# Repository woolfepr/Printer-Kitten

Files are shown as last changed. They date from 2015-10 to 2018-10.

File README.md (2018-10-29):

# Kitten
Portable, Accurate, Open Source 3D Printer

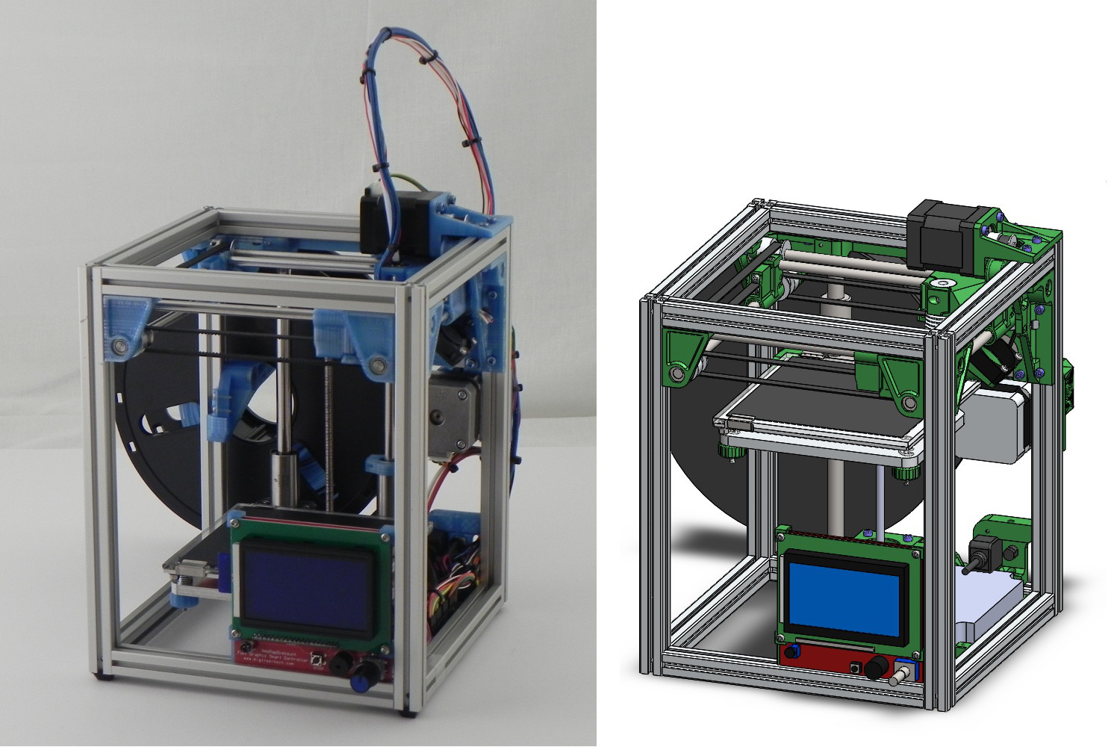
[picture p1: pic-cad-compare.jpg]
Comparing CAD model and real life Kitten Printer


## Printer Kitten Design Story
#### 3/31/16 - *Patrick Woolfenden*

The first printer I built was Sublime’s Tantillus. The Tantillus’ small size and print quality are what drew me to it. The Ultimaker Style X and Y axes motion system were fascinating. For me, the Tantillus turned out to be a great first printer. It wasn’t the easiest to put together and I had to source all of the parts myself, but in the end it didn’t disappoint delivering exceptional print quality.

Inspired by the Tantillus and the other T-Slot Tantillus and Ultimaker style printers, such as Brad Hill’s T-Slot Tantillus, Tim Rastall’s Ingentus, and Eric Lien’s HurcuLien, I set off to design my own version. This printer had a 200mm X 200mm print area and was roughly the same size as the Ultimaker. It used a 20mm extrusion frame, and toothed belts where the Tantillus had used high tension fishing line. After meeting Martin Bondėus at the 2015 MidWest RepRap Festival I decided to try the Bondtech extruder. It proved to be much more consistent and reliable than the Tantillus extruders I was used to. The printer worked well and produced great prints, but had its own set of issues. It remains unreleased, as I don’t think it’s ready for other people to try to build. It work well and had many unique design features that found their way to the Kitten.

The next printer I designed was the Kitten. Reflecting back to Midwest RepRap Festivals I had attended, I remembered how the Tantillus intrigued people because of its small compact design. I decided to make my next printer compact and portable.

I enjoyed the challenge of trying to package all of the printer components into the smallest and spatially efficient layout I could. In order to make the printer very compact the Kitten was first laid out with all of the X and Y-axes, print head, and frame purchased parts positioned in space. I iterated, trying different motor sizes and positions, rod diameters, bearing sizes, etc., keeping in mind that I would be designing printed parts to hold parts together. I decided on a 15mm T-slot extrusion [extruder or extrusion?], Nema 14, and E3D lite hot end. After feeling happy about the compact packaging layout, I began designing the printed part for the printhead. Once that was roughly designed I moved onto the rest of the X and Y-axes, making slight tweaks to the component layout as necessary. A clever way to tension the belts is key to the Kitten’s compact design. To fit in the small space available, hall effect switches are used for end stops. At this point I was confident that the frame foot print would be a 200mm square with a 100mm square print area. The X and Y-axes and printhead were the most challenging parts of the printer, with the goal of as small of a foot print as possible. 

For the Z-axis I opted for a simple cantilevered bed. 10mm rods and flanged linear bearings were used because they were the largest that could fit without increasing the size of the printer. Three oversized parts make the Kitten’s small bed very sturdy. A Nema 14 stepper motor with an integrated lead screw is used to move the bed. In order to keep it simple and stiff I decided to make the bed out of 2 metal plates. A silicone heated pad is used for bed heating. Leveling the bed is easy with 3 adjustment nuts. 

The Ultimachine mini-rambo was a great fit for the Kitten’s control electronics because of its ease of use, low profile, and small foot print. I stuck with the Bondtech V2 extruder for the Kitten. While the Kitten uses Nema 14 motors for the X, Y, and Z-axes, it still uses the standard Nema 17 for the extruder. I designed a pivoting spool holder that can be folded away to retain the Kitten’s small size for travel. Since the first Kitten, the printed parts have gone through many iterations. All of the printed parts of the Kitten have been designed so that printing without support material is possible. One part has a break way support modeled directly into the STL file. 

During the couple of months leading up to the 2016 Midwest RepRap Festival I built 2 more Kittens and made a kit for a friend, who built his own and provided me feedback. My friend Matt Skorina and I traveled to the Midwest RepRap Festival with 3 Kittens, reading to debut them to the 3D printing community.

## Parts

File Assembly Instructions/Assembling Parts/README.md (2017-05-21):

# Kitten Assembly Instructions

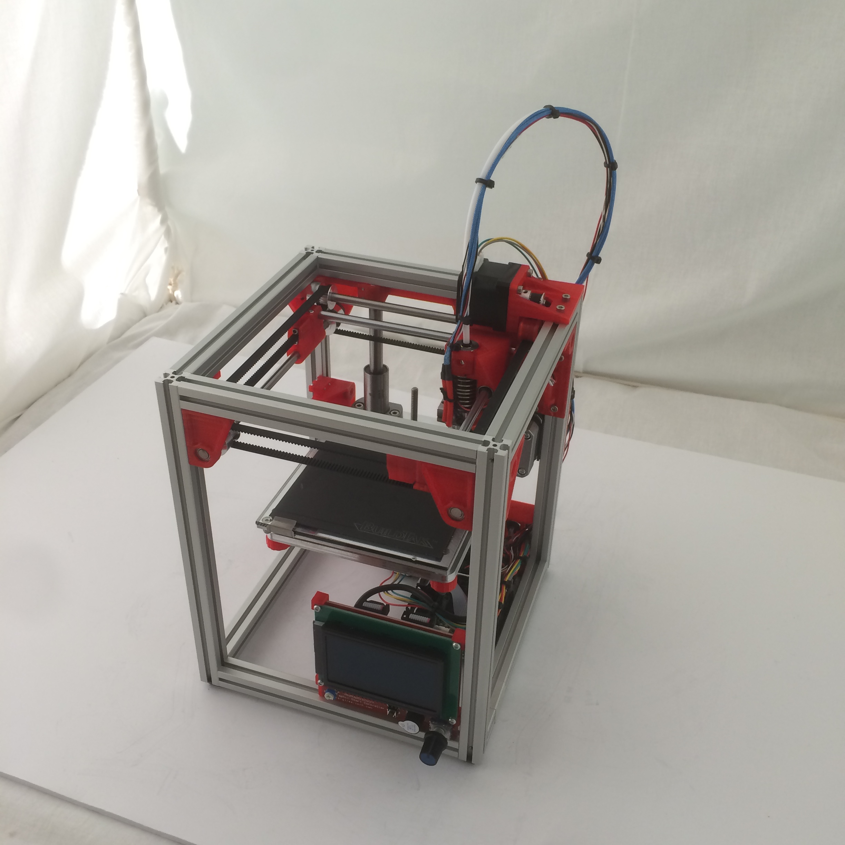
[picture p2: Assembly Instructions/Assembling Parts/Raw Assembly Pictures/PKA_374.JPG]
Assembly Picture


# Upper Back Right Corner

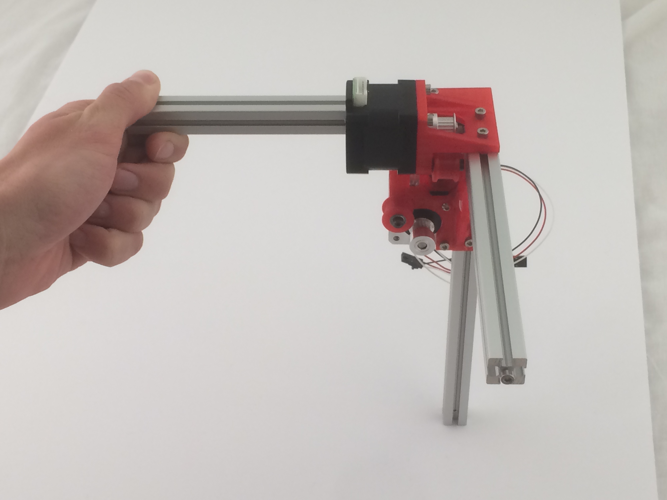
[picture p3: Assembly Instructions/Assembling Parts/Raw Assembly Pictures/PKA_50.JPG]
Assembly Picture


## Y End Stop

Upper back right printed part

Shorter end stop wire (1 of 2, mini rambo box)

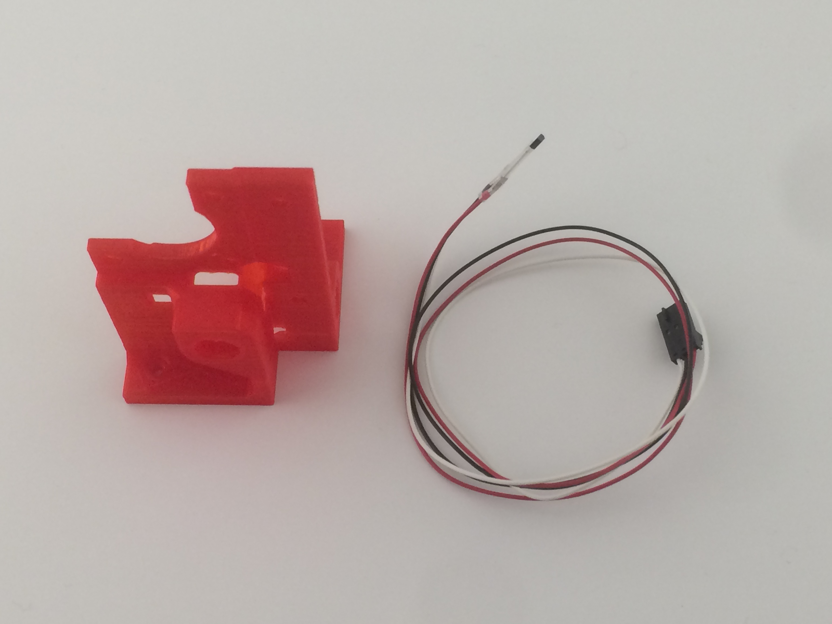
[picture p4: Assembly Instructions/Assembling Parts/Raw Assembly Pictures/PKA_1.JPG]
Assembly Picture


It is important the wire goes through the hole as shown

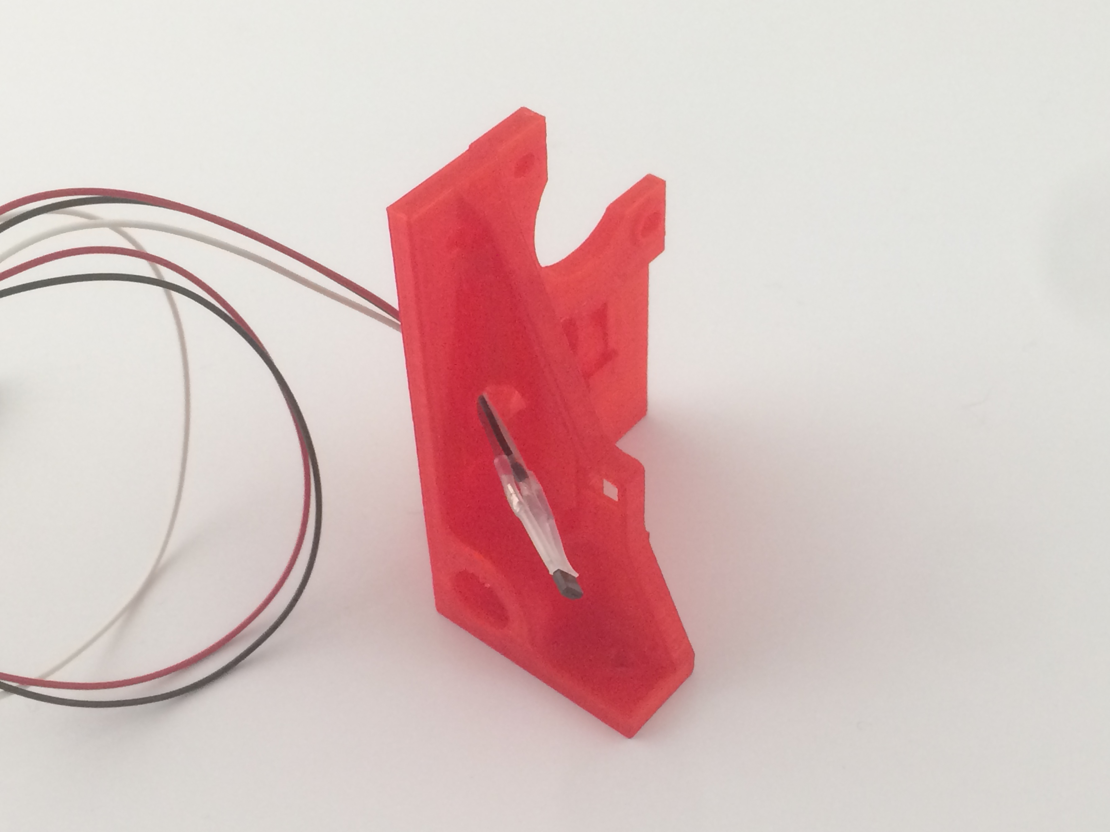
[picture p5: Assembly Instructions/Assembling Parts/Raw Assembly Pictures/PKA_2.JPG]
Assembly Picture


Feed through the other hole as shown

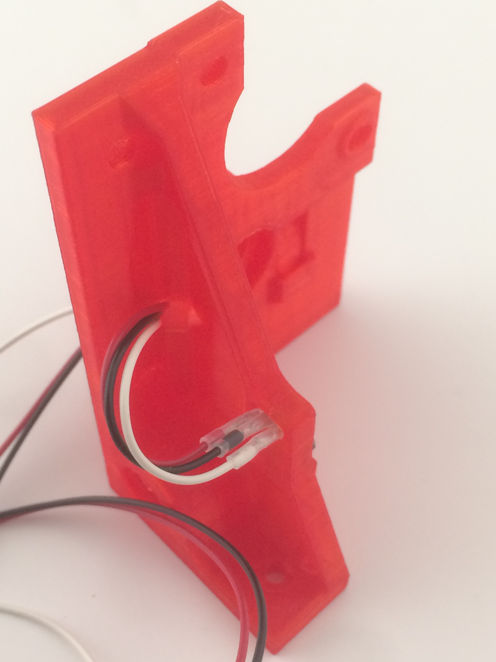
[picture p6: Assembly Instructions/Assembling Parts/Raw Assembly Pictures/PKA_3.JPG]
Assembly Picture


Orient the sensor so the smaller flat side (with text) is **not** against the plastic.

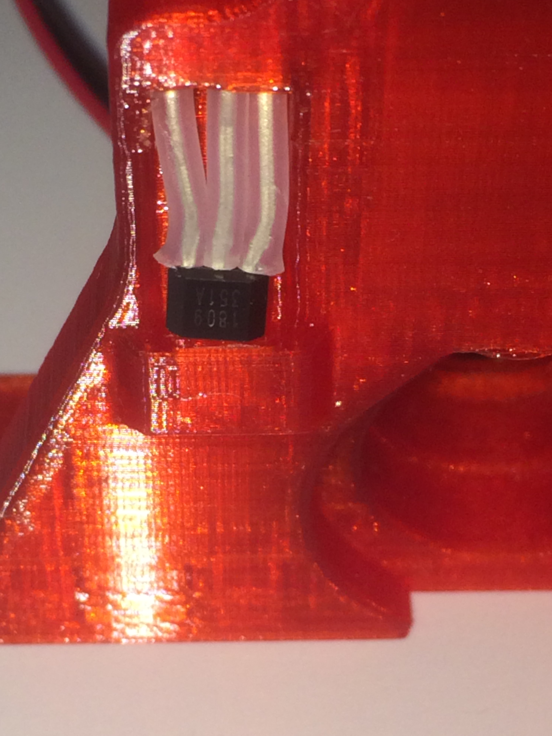
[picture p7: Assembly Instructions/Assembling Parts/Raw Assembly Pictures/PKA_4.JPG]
Assembly Picture


Push the sensor down until it is in the pocket. Use a drop of medium or thick viscosity super glue to glue the sensor in the pocket (recommended).

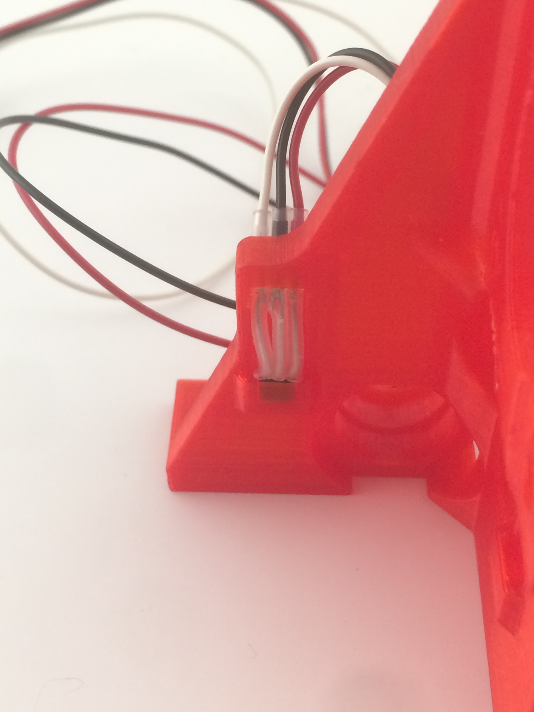
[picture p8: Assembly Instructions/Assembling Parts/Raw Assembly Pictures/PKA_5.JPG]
Assembly Picture


## X End Stop

Upper back right corner you just prepared

Shorter end stop wire (mini rambo box)

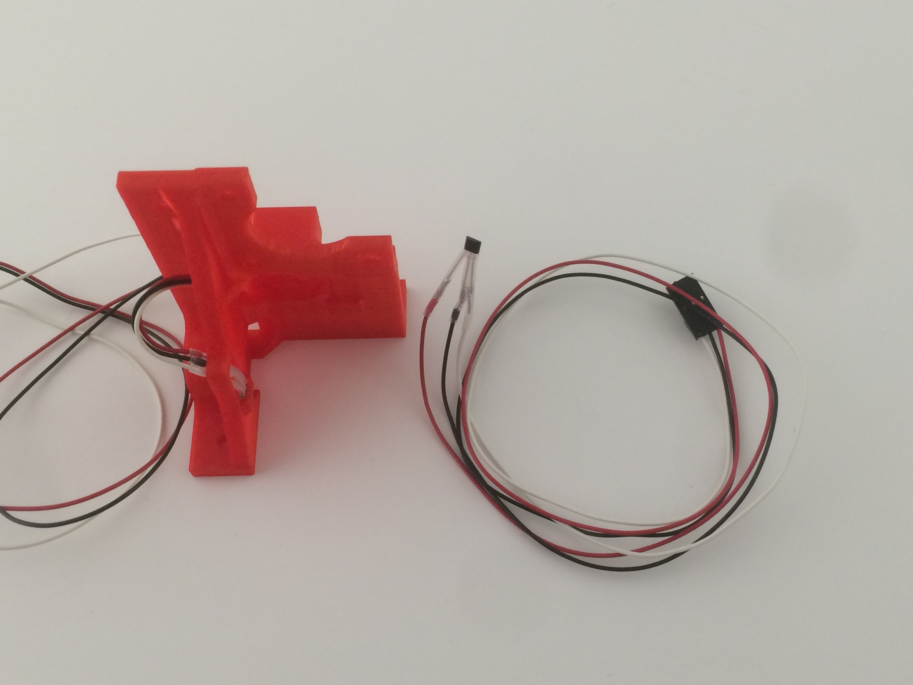
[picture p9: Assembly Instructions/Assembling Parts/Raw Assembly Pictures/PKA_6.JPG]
Assembly Picture


Feed the end stop sensor through this hole as shown.

Assembly Picture

Orient the sensor so the smaller flat side (with text) is **not** against the plastic.

Assembly Picture

Push the sensor down until it is in the pocket. Use a drop of medium or thick viscosity super glue to glue the sensor in the pocket (recommended).

## Bearings

Upper back right corner you just prepared

2 R188 bearings (larger bearing in bag 15)

Assembly Picture

Install bearings into the larger holes. Ensure bearings are fully seated. It can be helpful to press the bearings in with the back of a screwdriver.

Assembly Picture

## Frame Bolts

Upper back right corner you just prepared

5 M3x8 socket head cap screws (bag 1)

5 M3 square nuts (bag 11)

Assembly Picture

Place 5 screws in holes as shown and thread nuts onto them.

Assembly Picture

## Attach to Frame

Upper back right corner you just prepared

Longer extrusion

Assembly Picture

Slide extrusion along longest side of printed part. Feed the 3 nuts into the slots. Do not tighten the screws yet.

Assembly Picture

## Prepare Frame Rail

2 Shorter extrusion

4 M3x8 socket head cap screws (bag number 1)

Assembly Picture

Thread screws onto both end of rods. Leave about 2mm of spacing under screw cap.

Assembly Picture

## Make Frame Corner

Both shorter extrusions you just prepared

Longer extrusion attached to printed part you just prepared

(Picture omitted)

Slide shorter extrusion onto printed part as shown. Do not tighten the screws yet.

Assembly Picture

Slide the other shorter extrusion onto the remaining side and feed the one nut into the slots.

Assembly Picture

Slide the longer extrusion up so that the screw caps from the two shorter extrusions feed into the slots on the longer extrusion.

Assembly Picture

Use a 2.5mm allen key to tighten the screws in the extrusion. Insert the allen key through the drilled hole to tighten. As you tighten insure the extrusions are square and flush.

Assembly Picture

Tighten all 5 screws holding printed part on using the same 2.5mm allen key. Ensure part is flush with all 3 frame extrusions.

Assembly Picture

## X Axis Motor Thermal Pad

1 thermal pad (bag 19)

1 NEMA 14 motor (smaller motor)

Assembly Picture

Remover liner from both side of thermal pad and place on motor as pictured.

Assembly Picture

## X Axis Idler

2 684 bearings (smaller bearings in bag 15)

1 4mm spacer (bag 8)

1 M3 4x16 shoulder bolt (shorter bolt from bag 8)

1 Printed idler pulley

Assembly Picture

Put bearing into idler and slide shoulder bolt into bearing.

Assembly Picture

Put spacer onto the shoulder bolt so it is inside the idler.

Assembly Picture

Put bearing onto other side of idler

Assembly Picture

## Attach X Axis Motor

X Axis Motor you just prepared

Idler you just prepared

1 M3x8 button head cap screw (bag 3)

1 M3x8 socket head cap screw (bag 1)

Assembly Picture

Place motor as shown so thermal pad is against frame.

Assembly Picture 

Attach the idler as shown using a 2mm allen key.

Assembly Picture

Screw button head cap screw into hole as shown. Tighten with 2mm allen key.

Assembly Picture

Screw socket head cap screw into the remain hole. Tighten with 2.5mm allen key.

Assembly Picture 

## X Axis Motor Pulley

2 M3 set screws (bag 23)

1 16 tooth pulley (smaller pulley in bag 23)

Assembly Picture

Preinstall the set screws into the pulley as shown using 1.5mm allen key. It is recommended to use threadlock (Loctite Blue 242).

Assembly Picture

Slide pulley onto motor shaft aligning the belt guide with the idler and tighten.

Good

Assembly Picture

Bad

Assembly Picture

## Y Axis Idler

2 684 bearings (smaller bearings in bag 15)

1 4mm spacer (bag 8)

1 M3 4x20 shoulder bolt (longer bolt from bag 8)

1 Printed idler pulley

Assembly Picture

Put bearing into idler and slide shoulder bolt into bearing.

Assembly Picture

Put spacer onto the shoulder bolt so it is inside the idler.

Assembly Picture

Put bearing onto other side of idler

Assembly Picture

## Y Axis Motor Pulley

2 M3 set screws (bag 23)

1 16 tooth pulley (smaller pulley in bag 23)

1 NEMA 14 motor (smaller motor)

Assembly Picture 

Preinstall the set screws into the pulley as shown. It is recommended to use threadlock (Loctite Blue 242).

Assembly Picture

Install pulley onto motor. Do not tighten.

Assembly Picture

## Y Axis Motor Mounting

Y axis motor you just prepared

Y axis idler pulley you just prepared

3 M3x8 socket head cap screws (bag 1)

1 thermal pad (bag 19)

Y motor mount printed part

Assembly Picture

Place motor onto the printed part as shown and attach idler. Tighten idler with 2mm allen key. Make sure the connector is oriented as shown in the picture.

Assembly Picture

Screw 3 remaining socket head cap screws onto motor. Tighten with 2.5mm allen key.

Assembly Picture

Tighten pulley on motor shaft using 1.5mm allen key.  Ensure belt guide is aligned with idler.

Good

Assembly Picture

Bad

Assembly Picture

Remover liner from both side of thermal pad and place on motor as pictured.

Assembly Picture

## Attach Y Axis Motor Assembly

Y Axis Motor Assembly

3 M3x8 socket head cap screws (bag 1)

3 M3 square nuts (bag 11)

Assembly Picture 

Place Y motor assembly as shown.

Assembly Picture 

Slide nuts onto extrusion and align with holes on y axis motor assembly. Install screws and tighten each nut as it is aligned. It is helpful to use an allen key to slide the nut down the extrusion.

Assembly Picture

Assembly Picture 

# Upper Back Left Corner

Assembly Picture

## Z Axis Upper Rod Mount

3 M3x8 socket head cap screws (bag 1)

3 M3 square nuts (bag 11)

Z axis upper rod mount printed part

Assembly Picture 

Note that you use the correct printed part, correct part on left

Assembly Picture

Place screws in holes as shown and thread nuts onto them.

Assembly Picture

Slide assembly onto shorter extrusion as shown. The orientation of the part is important. Do not tighten.

Assembly Picture 

## Upper Back Left Corner

Upper back left corner printed part (listed as upper front right corner in BOM, but identical part)

4 M3x8 socket head cap screws (bag 1)

4 M3 square nuts (bag 11)

2 R188 bearings (larger bearing in bag 15)

Assembly Picture

Note that you use the correct printed part, good on left

Assembly Picture

Install bearings into the holes. Ensure fully seated.

Assembly Picture

Place screws in holes as shown and thread nuts onto them.

Assembly Picture

## Short Extrusion Sub Assembly

1 Shorter extrusion

2 M3x8 socket head cap screws (bag 1)

Assembly Picture

Thread screws onto both end of rod. Leave about 2mm of spacing under screw cap.

Assembly Picture

## Install Upper Back Left Corner

Shorter extrusion you just prepared

Upper back left corner you just prepared

Longer extrusion

Assembly Picture 

Slider longer extrusion along back corner of part. Feed the two nuts into the slots on the extrusion.

Assembly Picture

Slider the shorter extrusion along the part as shown. Feed the nut into the slot.

Assembly Picture

Slider the extrusion attached to the rest of the printer along the last remaining side. Feed the nut into the slot.

Assembly Picture 

Slide the longer extrusion up so that the screw caps from the two shorter extrusions feed into the slots on the longer extrusion. Use a 2.5mm allen key to tighten the screws in the extrusion. Insert the allen key through the drilled hole to tighten. As you tighten insure the extrusions are square and flush.

Assembly Picture

Tighten the four screws on the corner part with 2.5mm allen key. Ensuring the part is flush to all three extrusions.

Assembly Picture

Slide Z axis upper rod mount against the printer corner piece you just installed

Good

Assembly Picture 

Bad

Assembly Picture 

Tighten the three screws with 2.5mm allen key.

Assembly Picture

## Upper Front Right Corner

Assembly Picture

Upper Front Right Corner

Upper front right corner printed part

4 M3x8 socket head cap screws (bag 1)

4 M3 square nuts (bag 11)

2 R188 bearings (larger bearing in bag 15)

Assembly Picture

Note that you use the correct printed part, good on left

Assembly Picture

Install bearings into the holes. Ensure fully seated

Assembly Picture

Place screws in holes as shown and thread nuts onto them.

Assembly Picture

## Short Extrusion Sub Assembly

1 Shorter extrusion

2 M3x8 socket head cap screws (bag 1)

Assembly Picture

Thread screws onto both end of rod. Leave about 2mm of spacing under screw cap.

Assembly Picture 

## Install Upper Front Right Corner

Shorter extrusion you just prepared

Upper front right corner you just prepared

Longer extrusion

Assembly Picture 

Slider longer extrusion along back corner of part. Feed the two nuts into the slots on the extrusion.

Assembly Picture

Slider the shorter extrusion along the part as shown. Feed the nut into the slot.

Assembly Picture

Slider the extrusion attached to the rest of the printer along the last remaining side. Feed the nut into the slot.

Assembly Picture

Slide the longer extrusion up so that the screw caps from the two shorter extrusions feed into the slots on the longer extrusion. Use a 2.5mm allen key to tighten the screws in the extrusion. Insert the allen key through the drilled hole to tighten. As you tighten insure the extrusions are square and flush.

Assembly Picture

Tighten the four screws on the corner part with 2.5mm allen key. Ensuring the part is flush to all three extrusions.

Assembly Picture

# Upper Front Left Corner

Assembly Picture

## Upper Front Left Corner

Upper front left corner printed part

4 M3x8 socket head cap screws (bag 1)

4 M3 square nuts (bag 11)

2 R188 bearings (larger bearing in bag 15)

Assembly Picture

Install bearings into the holes. Ensure fully seated

Assembly Picture

Place screws in holes as shown and thread nuts onto them.

Assembly Picture 

## Install Upper Front Left Corner

Longer extrusion

Upper front left corner you just prepared

Assembly Picture 

Slider longer extrusion along back corner of part. Feed the two nuts into the slots on the extrusion.

Assembly Picture

Slide the assembly on the slot of the extrusion on the printer as shown.

Assembly Picture

Slide the remaining nut on the assembly onto the other extrusion on the printer.

Assembly Picture

Slide the longer extrusion up so that the screw caps from the two shorter extrusions feed into the slots on the longer extrusion. Use a 2.5mm allen key to tighten the screws in the extrusion. Insert the allen key through the drilled hole to tighten. As you tighten insure the extrusions are square and flush.

Assembly Picture

Tighten the four screws on the corner part with 2.5mm allen key. Ensuring the part is flush to all three extrusions.

(picture ommited)

# XY Axis Rods

Assembly Picture

## Rod Pulleys

8 20 tooth pulley (bag 23)

16 M3 set screws (bag 23)

Assembly Picture

Preinstall the set screws into the pulleys as shown using 1.5mm allen key.

Assembly Picture

## Magnets on XY Ends

2 xy end printed part

2 2mm x 1mm disc magnet (bag 13)

Assembly Picture

Glue magnets into the hole in the printed part as shown. Use medium or thick viscosity super glue.

Assembly Picture
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

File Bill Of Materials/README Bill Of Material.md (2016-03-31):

# Printer Kitten Bill of Materials

The bill of materials includes the parts required to build a Printer Kitten as well as recomended sources to buy them from.

Please keep in mind:
- Some of the items in the bill of materials are multiple of a certain part. This is most applicable to boxes of screws and other such hardware. If you order the recomended part number there will be extras of the part. Please keep this in mind if you plan to order parts for multiple printers.

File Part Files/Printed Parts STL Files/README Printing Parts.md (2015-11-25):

# Tips

If you plan on having a heated bed, I recommend not printing the print head out of PLA because of the fan shrouds proximity to the bed.

The parts for the extruder can be purchased from Bondtech. If you want to print your own, the files are available on the Bondtech website.

# Assemblies of Parts

The assemblies of parts can make it easier/faster to print Printer Kitten parts.
 
Printing all of the assemblies will make enough parts for a Kitten. 

The size of these assemblies are small enough to be printed on a Printer Kitten.

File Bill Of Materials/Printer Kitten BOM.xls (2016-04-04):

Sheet: Purchased Parts
Printer Kitten Purchased Parts
Part Description | Part# or SKU# | Estmated Cost Per Part | qty | ex cost | Source | Notes/ Recommendations
Motor, Stepper, NEMA14 X 44mm | MNEMA14-44 | $7.90 | 2 | $15.80 | robotdigg
Motor, Stepper, NEMA14 with Tr5*2 Acme Leadscrew | 14HY007-180T52 | $32.50 | 1 | $32.50 | robotdigg
Belt, GT2 6mm, Open Ended | GT2-6-OPEN | $1.80 | 2 | $3.60 | robotdigg | Order one 5-Meter Length for 3 printers
Fan, 25mm, 12V | E2510FAN | $1.80 | 1 | $1.80 | robotdigg
Motor, Stepper, Geared Nema17 | GNEMA17-34 | $27.00 | 1 | $27.00 | robotdigg
Pulley, GT2, 20 Tooth, 6.35mm Bore | GT2-20T-6.35B-6 | $1.85 | 8 | $14.80 | robotdigg
Pulley, GT2, 16 Teeth, 5mm Bore | GT2-16T | $1.80 | 2 | $3.60 | robotdigg | 5mm bore option
Bearing, 684ZZ, pack of 10 | BB683456 | $5.00 | 1 | $5.00 | Robotdigg | You will use 4 of these bearings
Screw, M3 x 8mm Socket Cap, Pack of 25 | SCS-M3-08 | $0.62 | 3 | $1.86 | trimcraftavationrc | You will use about 62 of these screws
Screw, M3 x 8mm Flat, Pack of 25 | 336 | $0.45 | 1 | $0.45 | trimcraftavationrc | You will use 4 of these screws
Screw, M3 x 8mm Button, pack of 25 | BSC_M3_8 | $0.61 | 1 | $0.61 | trimcraftavationrc | You will use 1 of these screws
Screw, M4 x 8mm Socket Cap, pack of 25 | SCS-M4-08 | $0.90 | 1 | $0.90 | trimcraftavationrc | You will use 4 of these screws
Screw, 4-40 x .625 Socket Cap, pack of 25 | SCS-440X5/8 | $0.47 | 1 | $0.47 | trimcraftavationrc | You will use 4 of these screws
Screw, 4-40 x 1.25 Socket Cap, pack of 12 | 147 | $0.49 | 1 | $0.49 | trimcraftavationrc | You will use 4 of these screws
Nut, M3, pack of 25 | PHN-M3 | $0.24 | 1 | $0.24 | trimcraftavationrc | You will use 6 of these nuts
Nut, M3 Lock, pack of 25 | NYLK-M3 | $0.39 | 1 | $0.39 | trimcraftavationrc | You will use 4 of these nuts
Washer, M3, pack of 25 | FW-M3 | $0.14 | 1 | $0.14 | trimcraftavationrc | You will use 3 of these washers
Washer, M3 Split Lock, pack of 25 | SLW-M3 | $0.16 | 1 | $0.16 | trimcraftavationrc | You will use 3 of these washers
Heat Shrink Tubing, 1/16" 1 foot | HST-1-16 | $0.49 | 1 | $0.49 | trimcraftavationrc | This is for the endstop hall switches
Screw, M3 x 30mm Flat, pack of 25 | 92125A140 | $5.06 | 1 | $5.06 | McMaster | You will use 3 of these screws
Screw, M2.63-1.06 X 10mm Torx, pack of 50 | 99397A416 | $9.92 | 1 | $9.92 | McMaster | You will use about 20 of these screws
Screw, M2.63-1.06 X 14mm Torx, pack of 50 | 99397A583 | $11.78 | 1 | $11.78 | McMaster | You will use about 24 of these screws
Screw, Shoulder M3 4 x 16 | 92981A144 | $2.35 | 1 | $2.35 | McMaster
Screw, Shoulder M3 4 x 20 | 92981A145 | $2.39 | 1 | $2.39 | McMaster
Spacer, 4 x 4mm | 94669A006 | $1.25 | 2 | $2.50 | McMaster
Spring, pack of 12 | 9657K288 | $10.35 | 1 | $10.35 | McMaster | You will usae 3 of these springs
Bumper, pack of 50 | 95495K24 | $5.85 | 1 | $5.85 | McMaster | You will use 4 of these bumpers
Glass, 5" x 5" x .125" | 8476K15 | $12.63 | 1 | $12.63 | McMaster
O-Ring, 011 Viton, pack of 100 | 9464K16 | $6.32 | 1 | $6.32 | McMaster | You will use 1 of these O-rings
Zip Tie, 4", pack of 100 | 7130K52 | $2.43 | 1 | $2.43 | McMaster
Shaft, 10mm | SFJ10-210 | $8.44 | 2 | $16.88 | misumi
Shaft, 6mm | PSFJ6-164 | $6.60 | 2 | $13.20 | misumi
Bearing, Linear, 6 x 10 x 35mm | LMKW6 | $13.35 | 2 | $26.70 | misumi | I do not recommend buying cheap Chineese linear bearings.
Bearing, Linear, flange, 10 x 19 x 47mm | LHICD10 | $9.82 | 2 | $19.64 | misumi | I do not recommend buying cheap Chineese linear bearings.
Nuts, Square, m3, pack of 100 | HNSQ3-3 | $8.28 | 1 | $8.28 | misumi | You will use about 32 of these nuts
Frame, Aluminum, 3 series 240mm | HFS3-1515-240 | $2.64 | 4 | $10.56 | misumi
Frame, Aluminum, 3 series 170mm | HFS3-1515-170 | $2.64 | 8 | $21.12 | misumi
Shaft, 0.25 X 7.75in | U-SFJ0.25-L7.75 | $4.20 | 4 | $16.80 | misumi
Mini-Rambo 1.3 | UMMINIRAMBOPAC13 | $120.00 | 1 | $120.00 | ultimachine | get with Optical Endstop Kits w/ Wiring so you get the correct endstop wires
Hot End, E3D Lite6 Full Kit - 1.75mm Universal (with Bowden add-on) (12v) | NA | $40.00 | 1 | $40.00 | e3d-online
Extruder, Bondtech, V2 1.75 Mechanical Kit | NA | $60.00 | 1 | $60.00 | Bondtech | shop.Bondtech.se
Adapter Direct - Bowden 1.75 | NA | $7.90 | 1 | $7.90 | Bondtech | shop.Bondtech.se
Omnipolar Hall Switch | AH1809-P-B-ND | $0.76 | 3 | $2.28 | digikey
Thermal Pad, Gap Pad GP1500-0.060 | BER228-ND | $39.76 | 1 | $39.76 | digikey | You will have lots of extra if you buy this sheet of thermal pad. Less expensive cut to size pads will be available on printerkitten.com
Full Graphic Smart LCD Controller | 12864LCD | $69.00 | 1 | $69.00 | reprapdiscount | You can find this for a much better price just be wary of the quality of knock offs
USB B Extension, 30cm, Female to Male, Panel Mount, 90°Right Angle | NA | $3.00 | 1 | $3.00 | aliexpress | You want to make sure you are getting the correct style
Bed Clip, UM2 | NA | $2.00 | 3 | $6.00 | aliexpress
Bearing, R188 | R188-ZZ | $3.75 | 8 | $30.00 | bocabearings | Less expensive high quality bearings are available, but Boca Bearings will for sure be good
Heater Pad, with Thermister, 4"X4", 100W 12V | NA | $24.99 | 1 | $24.99 | ebay user Keenovo | (Optional) ebay user Keenovo
DC Power Jack, Panel Mount, 5.5mm x 2.1mm, pack of 15 | NA | $6.99 | 1 | $6.99 | ebay user weisschang2011 | you only need one of these
Power Supply, 12V | NA | $30.00 | 1 | $30.00 | ebay | >5Amp no heated bed , >12Amp with 100watt bed, >9Amp 50watt bed
N50. 3mm x 1 mm Disc Magnet | D1007 | $0.19 | 3 | $0.57 | SuperMagnetMan
BuildTak, 4.5" x 4.5" Square, Black (Pack of 3) | NA | $9.35 | 1 | $9.35 | Amazon
Z-Axis Frame | NA | $50.00 | 1 | $50.00 | machine shop? | This is one 1 of 2 not off the shelf parts for the printer. Will be available on printerkitten.com Drawings are available if you wish to source/make your own.
Z-Axis Bed | NA | $50.00 | 1 | $50.00 | machine shop? | This is one 1 of 2 not off the shelf parts for the printer. Will be available on printerkitten.com Drawings are available if you wish to source/make your own.
 | Total Purchased Parts Cost |  |  | $864.90
Usefull tools you may consider buying
Torx L-Key, T8 | 6959A14 | $2.13 | 1 | $2.13 | McMaster | This is usefull for the plastic threadforming screws

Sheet: Printed Parts
Printed Parts
File name | Qty
Printed Part, Corner, Upper Front Right | 2
Printed Part, Corner, Upper Back Right | 1
Printed Part, Corner, Upper Front Left | 1
Printed Part, Y Motor Mount | 1
Printed Part, Z Axis Upper Rod Mount | 1
Printed Part, Z Axis Lower Rod Mount | 1
Printed Part, Z End Stop Magnet Mount | 1
Printed Part, Z End Stop Mount | 1
Printed Part, Z Motor Mount | 1
Printed Part, BondTech Clamp 1 | 1
Printed Part, BondTech Clamp 2 | 1
BondTech Housing V2 Front 1.75 | 1
BondTech Housing V2 Rear | 1
Printed Part, Z Adjustment Nut | 3
Printed Part, IO Mount | 1
Printed Part, X&Y End | 4
Printed Part, Print Head Body | 1
Printed Part, Print Head Clamp | 1
Printed Part, Spool Holder Part1 | 1
Printed Part, Spool Holder Part4 | 1
Printed Part, Spool Holder Part2 | 1
Printed Part, Spool Holder Part3 | 1
Printed Part, LCD Mount 1 | 1
Printed Part, LCD Mount 2 | 1
Printed Part, LCD Mount 3 | 1
Printed Part, LCD Mount 4 | 1
Printed Part, Rambo Mini Mount 1 | 2
Printed Part, Rambo Mini Mount 2 | 1
Printed Part, X&Y Belt Guide | 2
Printed Part, X&Y Spacer | 8
Printed Part, X&Y End Belt Clamp 1 | 4
Printed Part, X&Y End Belt Clamp 2 | 4
Printed Part, X&Y End Belt Clamp 3 | 4
total Printed parts | 57

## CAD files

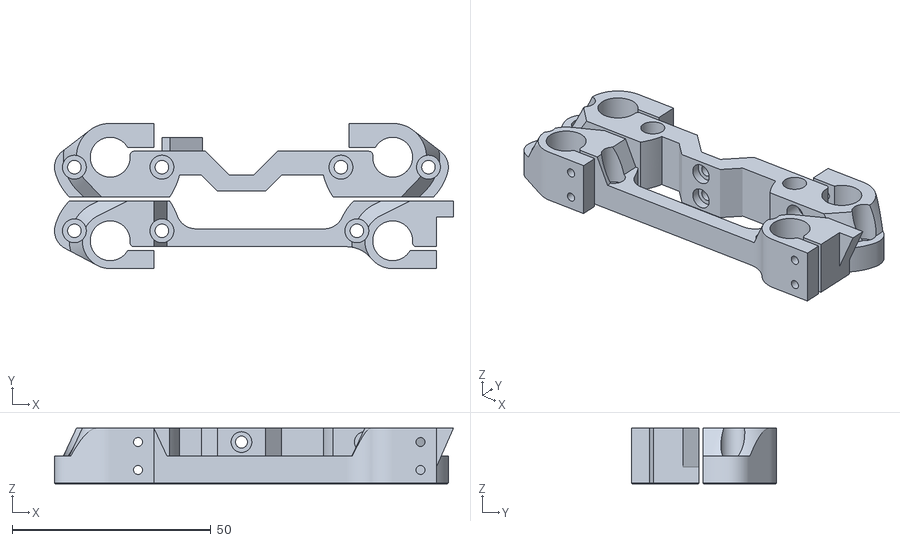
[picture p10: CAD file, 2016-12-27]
Part Files/Printed Parts STL Files/Assemblies of Parts/Print Assembly 3 Z Axis.STL
100.3 x 36.5 x 14.0

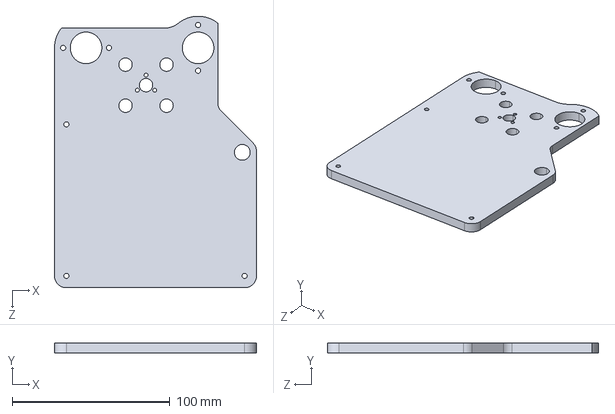
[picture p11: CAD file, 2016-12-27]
Part Files/Bed Plates/Z Axis Frame REV2.IGS
128.0 x 6.35 x 172.0 mm

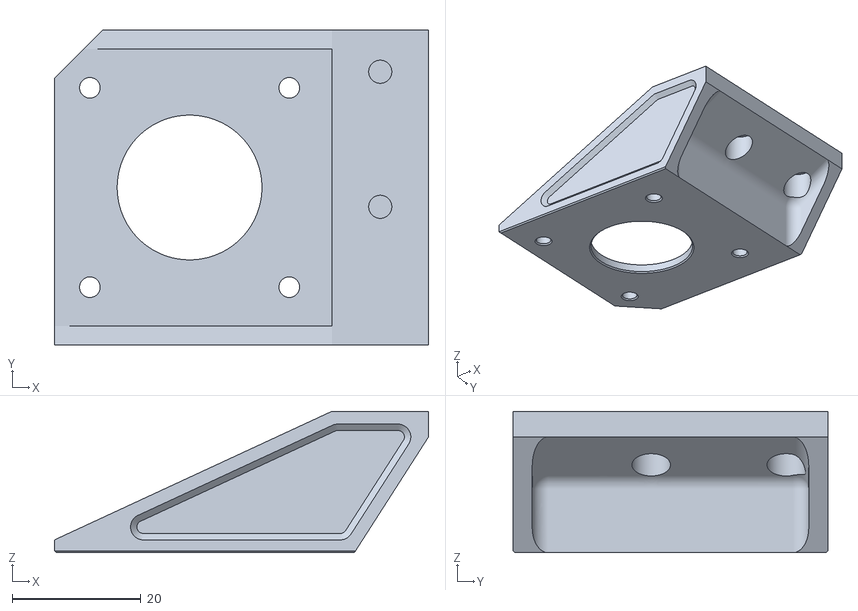
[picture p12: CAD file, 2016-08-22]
Part Files/Printed Parts STL Files/Printed Part, Titan Mount.STL
58.2 x 49.0 x 22.0

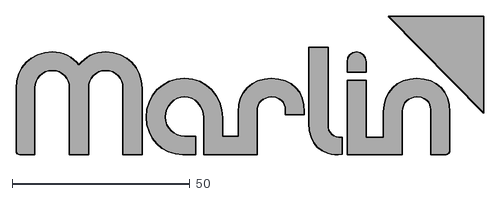
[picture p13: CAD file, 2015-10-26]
Software/Firmware/Marlin-1.0.2-Printer-Kitten/Documentation/Logo/Marlin Logo.dxf
131.6 x 39.5

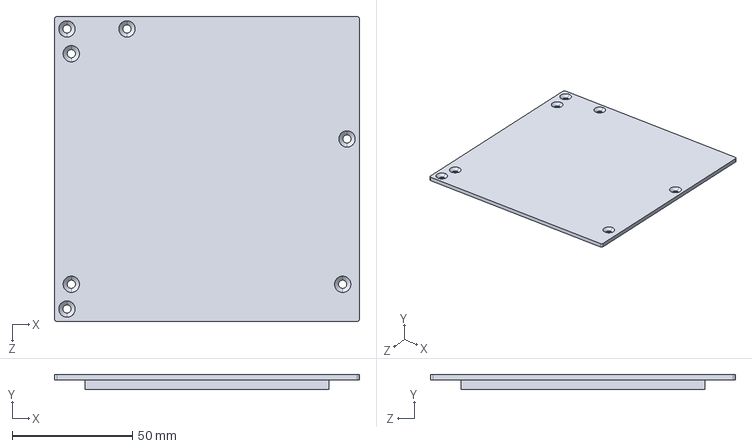
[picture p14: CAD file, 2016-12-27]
Part Files/Bed Plates/Z Axis Bed REV3.IGS
127.0 x 6.35 x 127.0 mm

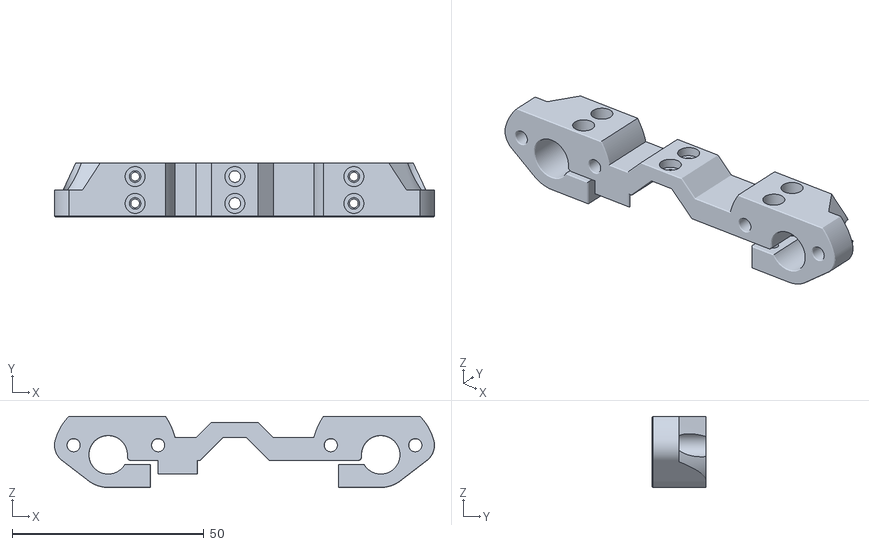
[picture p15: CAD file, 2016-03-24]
Part Files/Printed Parts STL Files/Printed Part, Z Axis Lower Rod Mount.STL
99.0 x 14.0 x 18.5

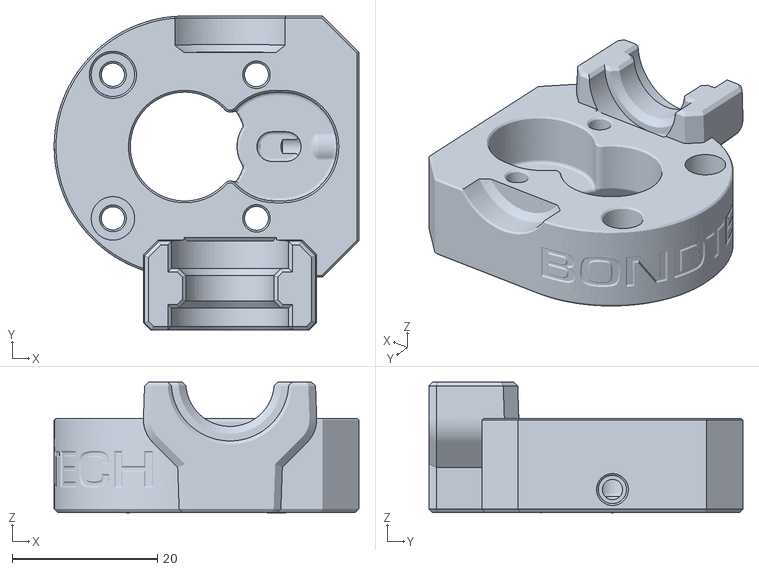
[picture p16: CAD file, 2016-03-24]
Part Files/Printed Parts STL Files/Bondtech Housing V2 Rear.STL
42.0 x 43.3 x 18.0

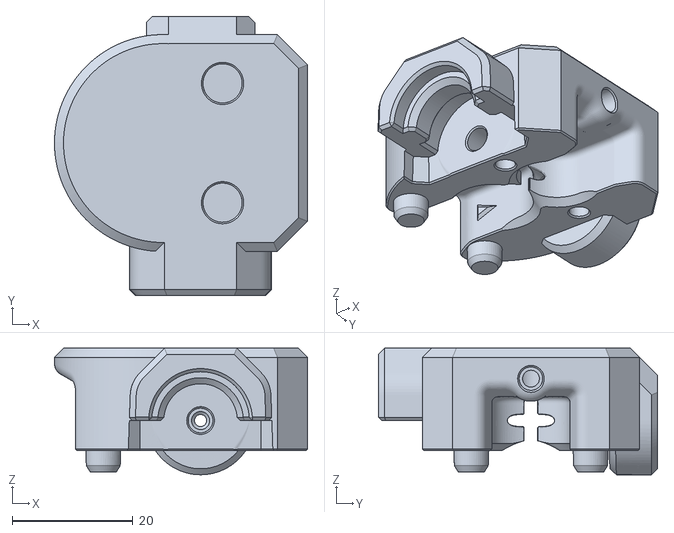
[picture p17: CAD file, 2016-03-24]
Part Files/Printed Parts STL Files/Bondtech Housing V2 Front 1.75.STL
42.0 x 46.3 x 21.0

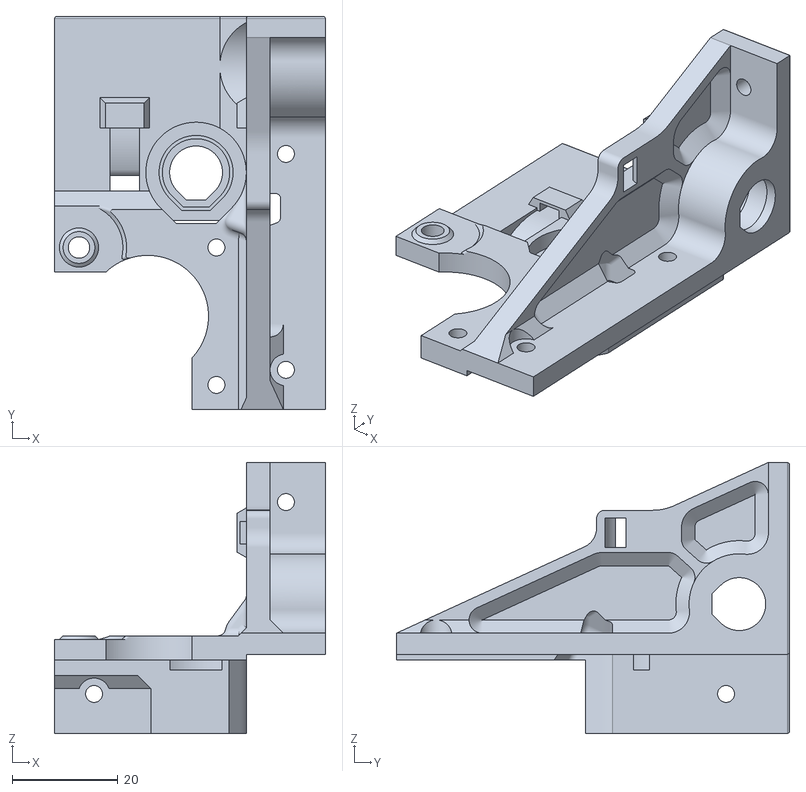
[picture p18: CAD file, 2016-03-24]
Part Files/Printed Parts STL Files/Printed Part, Corner, Upper Back Right.STL
51.3 x 74.3 x 51.3

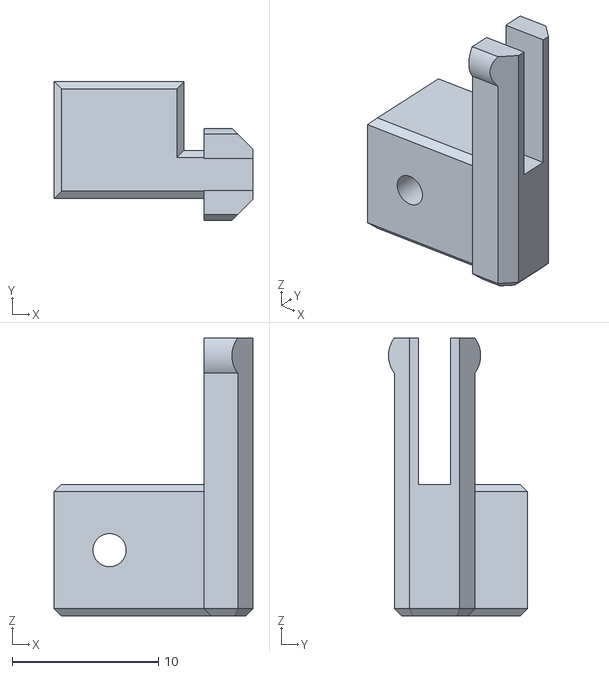
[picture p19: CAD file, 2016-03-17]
Part Files/Printed Parts STL Files/Printed Part, Rambo Mini Mount 1.STL
13.6 x 9.50 x 19.0

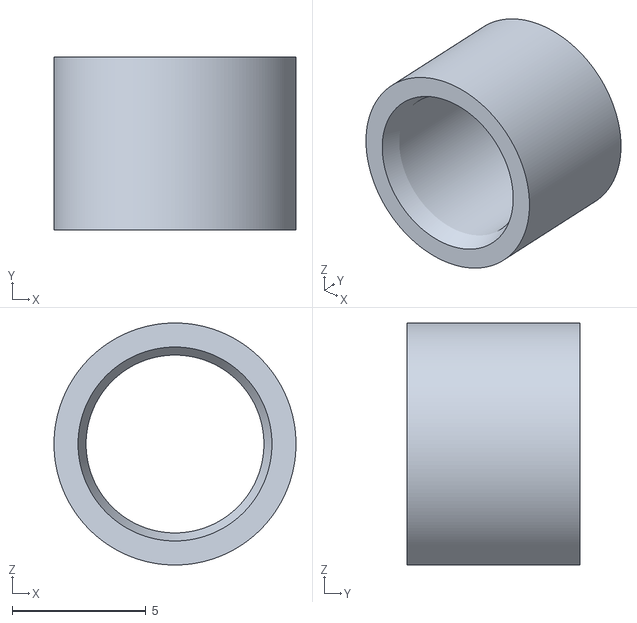
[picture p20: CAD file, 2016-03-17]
Part Files/Printed Parts STL Files/Printed Part, X&Y Spacer.STL
9.05 x 6.49 x 9.05

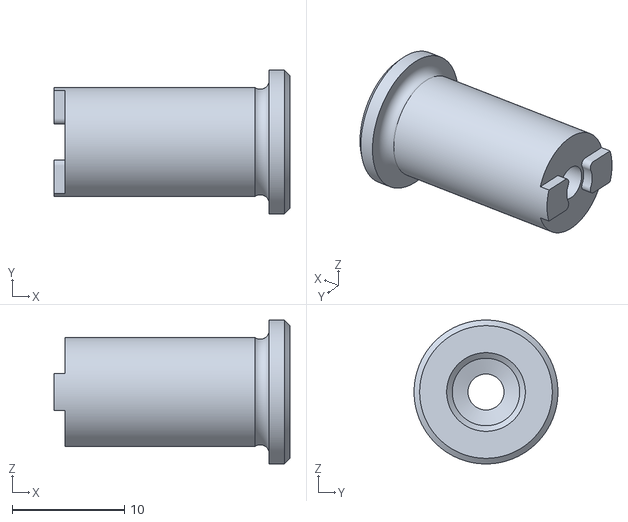
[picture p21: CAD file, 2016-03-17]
Part Files/Printed Parts STL Files/Printed Part, Spool Holder Part4.STL
21.0 x 12.8 x 12.8

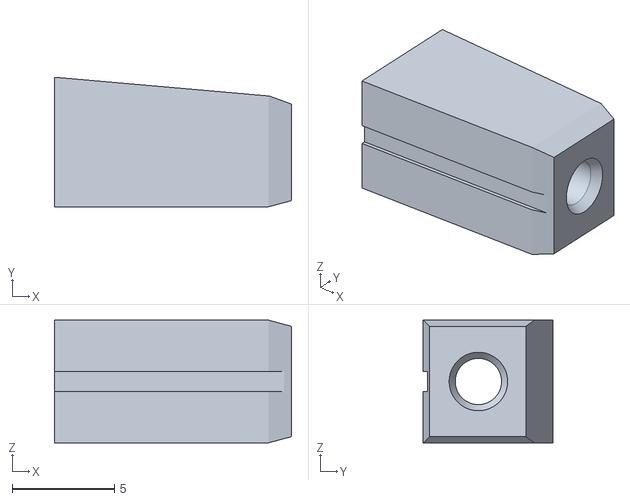
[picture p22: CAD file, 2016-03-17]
Part Files/Printed Parts STL Files/Printed Part, X&Y End Belt Clamp 1.STL
11.6 x 6.34 x 6.00

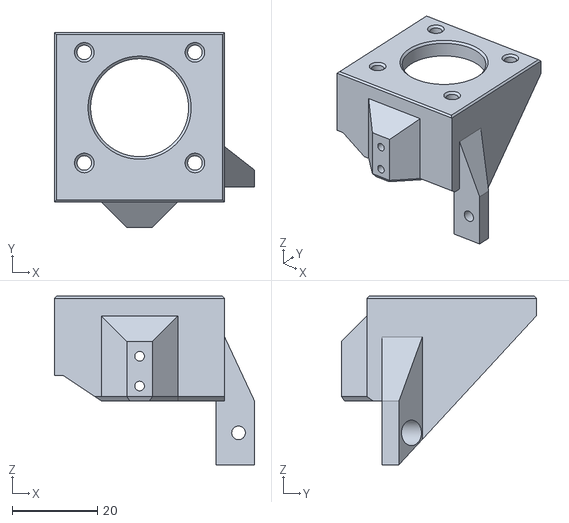
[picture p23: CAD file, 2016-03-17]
Part Files/Printed Parts STL Files/Printed Part, Z Motor Mount.STL
47.0 x 45.8 x 39.6

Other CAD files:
Part Files/Printed Parts STL Files/Printed Part, IO Mount.STL
Part Files/Printed Parts STL Files/Printed Part, Corner, Upper Front Left.STL
Part Files/Printed Parts STL Files/Printed Part, Print Head Clamp.STL
Part Files/Printed Parts STL Files/Printed Part, Z End Stop Magnet Mount.STL
Part Files/Bed Plates/Z Axis Bed REV3.x_t
Part Files/Bed Plates/Z Axis Frame REV2.x_t
Part Files/Printed Parts STL Files/Printed Part, BondTech Clamp 1.STL
Part Files/Printed Parts STL Files/Printed Part, BondTech Clamp 2.STL
Part Files/Printed Parts STL Files/Printed Part, Corner, Upper Front Right.STL
Part Files/Printed Parts STL Files/Printed Part, LCD Mount 1.STL
Part Files/Printed Parts STL Files/Printed Part, LCD Mount 2.STL
Part Files/Printed Parts STL Files/Printed Part, LCD Mount 3.STL
Part Files/Printed Parts STL Files/Printed Part, LCD Mount 4.STL
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

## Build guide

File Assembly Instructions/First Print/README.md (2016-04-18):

# First Print

## Load your PLA filament

Manually move the bed down so the nozzle is not to close to the bed

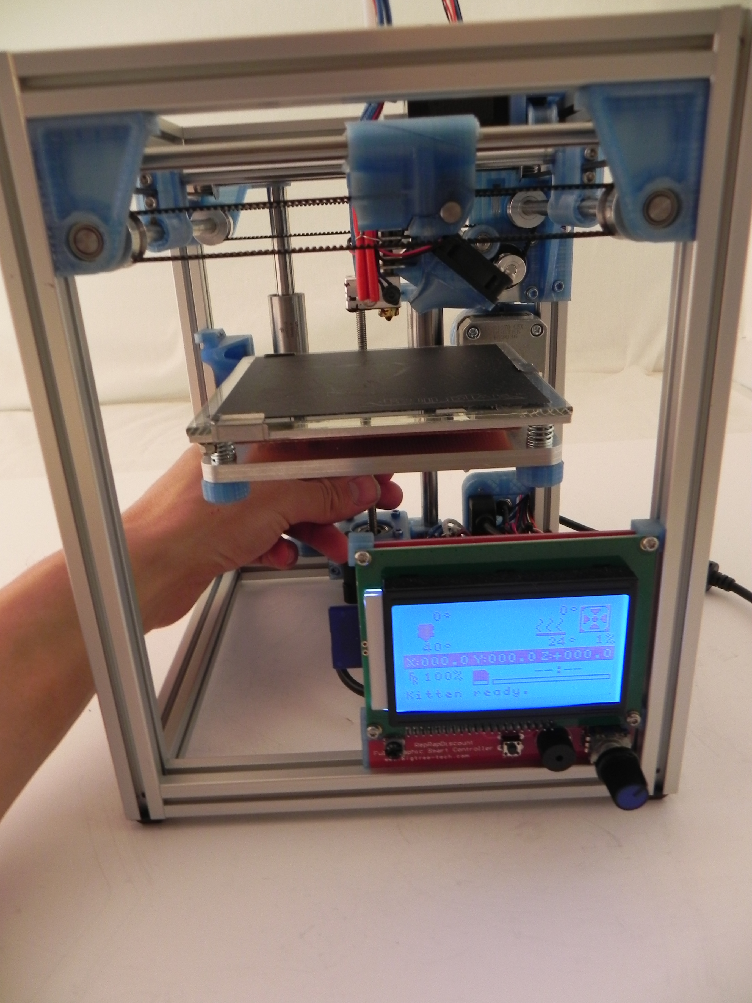
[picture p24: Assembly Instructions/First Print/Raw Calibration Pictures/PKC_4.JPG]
Calibration Picture


Preheat the nozzle by navigating on the LCD controller to prepare, then preheat PLA, then preheat PLA 1. Wait until the nozzle is up to more than 180 degrees C.

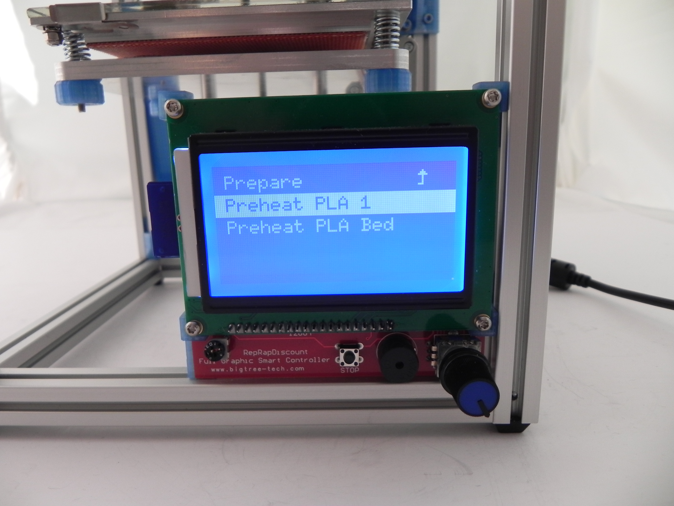
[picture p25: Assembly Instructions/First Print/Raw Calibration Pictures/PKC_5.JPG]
Calibration Picture


Cut off the tip of the filament if needed (if the end of the filament is not clean, is bent, or has a molten blob).  Mount the spool on the spool holder and feed the tip of the filament into the bottom of the extruder.

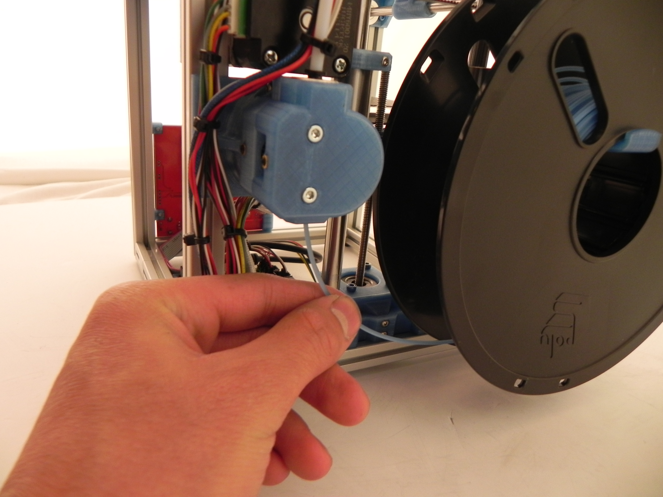
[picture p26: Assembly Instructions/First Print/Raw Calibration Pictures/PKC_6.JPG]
Calibration Picture


Holding the filament into the extruder, navigate on the LCD to prepare, and then load filament. The extruder should feed the filament up through the Bowden tube.

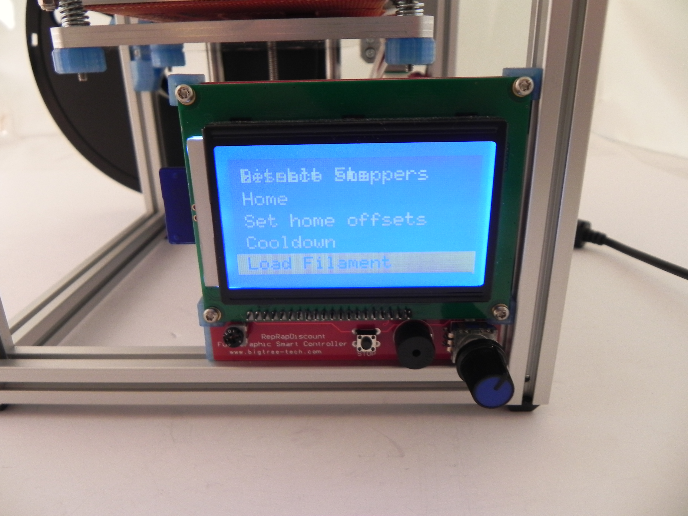
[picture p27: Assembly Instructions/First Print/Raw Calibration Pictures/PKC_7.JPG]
Calibration Picture


Navigate to prepare, then purge 5mm on the LCD. Purge 5mm until the filament is flowing smoothly out of the nozzle. (It doesn’t hurt to purge a little more than you probably need  in order to ensure all the air bubbles in the nozzle have come out)

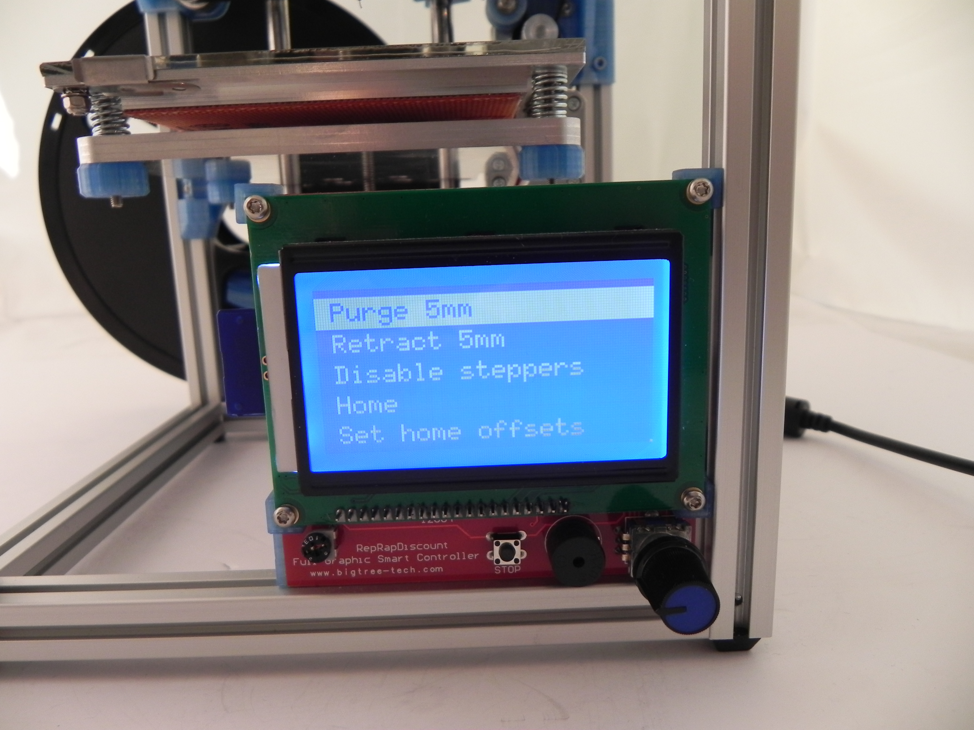
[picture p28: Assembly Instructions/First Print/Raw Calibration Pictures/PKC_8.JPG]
Calibration Picture


Navigate to prepare, then cooldown.

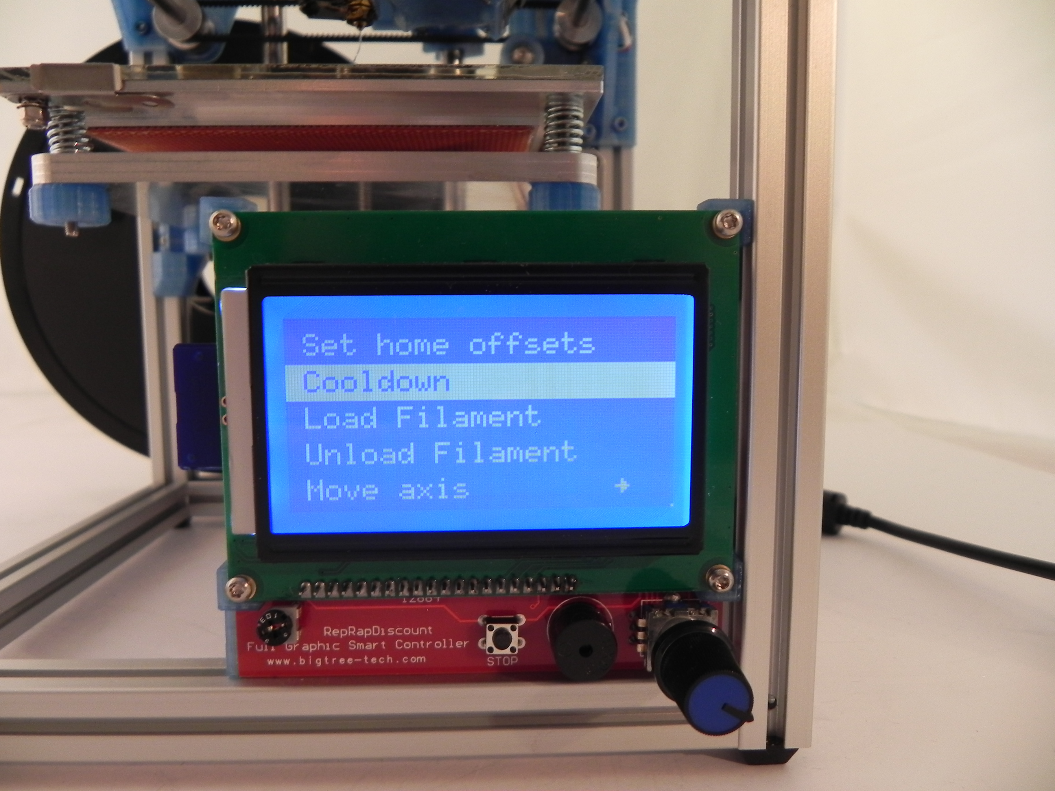
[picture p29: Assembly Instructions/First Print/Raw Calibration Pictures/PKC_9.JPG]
Calibration Picture


## First Print

There is gcode file (no slicer needed) ready to go for a first print. [FirstPrint_3DBenchy.gcode](https://github.com/woolfepr/Printer-Kitten/blob/master/Assembly%20Instructions/First%20Print/FirstPrint_3DBenchy.gcode) Simply put it on the SD card, navigate to print from SD, and select it. Your printer should heat up and successfully print for the first time.

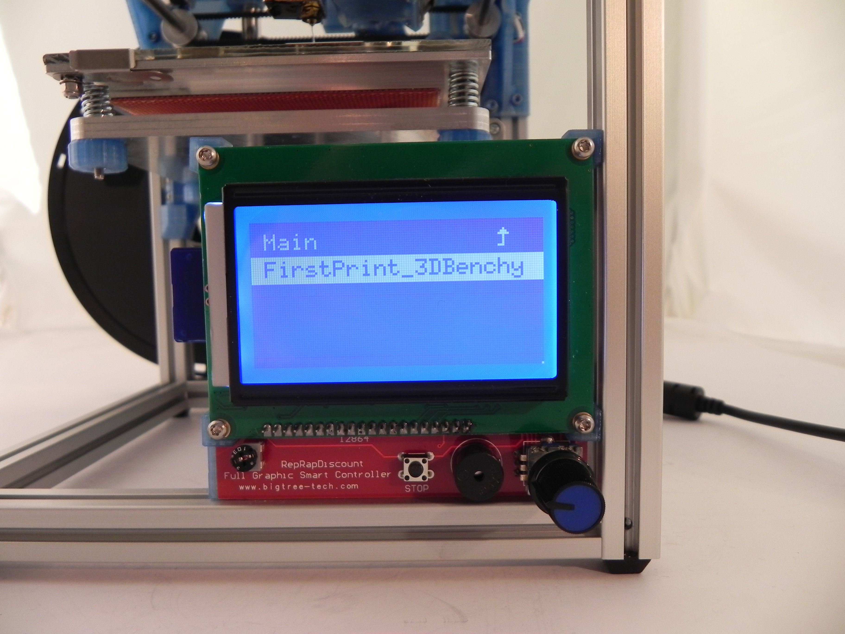
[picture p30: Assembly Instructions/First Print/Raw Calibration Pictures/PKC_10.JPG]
Calibration Picture


Once the first print is finished and you are ready to print items of your own choice or design you will need to begin using a slicer/ tool pathing program. I recommend using [Cura by Ultimaker](https://ultimaker.com/en/products/cura-software). Download and install the latest version.

The profile I have fine-tuned to run PLA on the kitten is available on Github. [Kitten 1.75.ini](https://github.com/woolfepr/Printer-Kitten/blob/master/Software/Cura%20Profile/Kitten%201.75.ini)  This profile should be a good starting point as far as tuning. You will want to play with the settings in order to get the best results on different models.

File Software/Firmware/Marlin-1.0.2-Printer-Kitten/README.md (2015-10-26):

Current Status: Bug Fixing
===================

What bugs are we working on: https://github.com/MarlinFirmware/Marlin/milestones/Bug%20Fixing%20Round%201

IRC channel on freenode: #marlin-firmware

(baaaah, #marlin was taken)

If a google hangout is needed then use this link: 

https://plus.google.com/hangouts/_/event/cps5d0ru0iruhl6ebqbk9dpqpa4?authuser=0&hl=da

It's valid for the next 10 years, must remember to renew then :-P

Developer Notes
===================

- There are now 2 branches: The __development__ branch is where new features and code changes will be sorted out. This branch may have untested code in it, so please let us know if you find any bugs. When the __development__ branch has reached a state where it is stable, it will be moved to the __stable__ branch.

- We are doing a kind of cleanup in the list of Issues and Pull Requests, the aim is to get to a state where we can certify the code as stable. To get the code tested as widely as possible we require several volunteers with a wide variety of hardware configurations willing to test the firmware and help us to certify it as stable. If you want to help out testing go to this issue and let us know: https://github.com/MarlinFirmware/Marlin/issues/1209

- Before you submit any pull request, we ask that you _PLEASE_ test your code before submission, even if the change seems innocuous. When creating the pull request, please include the hardware you used for testing and a short synopsis of your testing procedure. Untested pull requests are less likely to be merged, as even slight changes create the risk of breaking the main branch.

- If you have a fix don't open an issue telling about it, but test the code and submit a pull request. Use the __development__ branch when you submit.

==========================
Marlin 3D Printer Firmware
==========================



Marlin has a GPL license because I believe in open development.
Please do not use this code in products (3D printers, CNC etc) that are closed source or are crippled by a patent.



Quick Information
===================
This RepRap firmware is a mashup between <a href="https://github.com/kliment/Sprinter">Sprinter</a>, <a href="https://github.com/simen/grbl/tree">grbl</a> and many original parts.

Derived from Sprinter and Grbl by Erik van der Zalm.
Sprinters lead developers are Kliment and caru.
Grbls lead developer is Simen Svale Skogsrud. Sonney Jeon (Chamnit) improved some parts of grbl
A fork by bkubicek for the Ultimaker was merged, and further development was aided by him.
Some features have been added by:
Lampmaker, Bradley Feldman, and others...

Features:
=========

*   Interrupt based movement with real linear acceleration
*   High steprate
*   Look ahead (Keep the speed high when possible. High cornering speed)
*   Interrupt based temperature protection
*   preliminary support for Matthew Roberts advance algorithm
    For more info see: http://reprap.org/pipermail/reprap-dev/2011-May/003323.html
*   Full endstop support
*   SD Card support
*   SD Card folders (works in pronterface)
*   SD Card autostart support
*   LCD support (ideally 20x4)
*   LCD menu system for autonomous SD card printing, controlled by an click-encoder.
*   EEPROM storage of e.g. max-velocity, max-acceleration, and similar variables
*   many small but handy things originating from bkubicek's fork.
*   Arc support
*   Temperature oversampling
*   Dynamic Temperature setpointing aka "AutoTemp"
*   Support for QTMarlin, a very beta GUI for PID-tuning and velocity-acceleration testing. https://github.com/bkubicek/QTMarlin
*   Endstop trigger reporting to the host software.
*   Updated sdcardlib
*   Heater power reporting. Useful for PID monitoring.
*   PID tuning
*   CoreXY kinematics (www.corexy.com/theory.html)
*   Delta kinematics
*   SCARA kinematics
*   Dual X-carriage support for multiple extruder systems
*   Configurable serial port to support connection of wireless adaptors.
*   Automatic operation of extruder/cold-end cooling fans based on nozzle temperature
*   RC Servo Support, specify angle or duration for continuous rotation servos.
*   Bed Auto Leveling.
*   Support for a filament diameter sensor, which adjusts extrusion volume

The default baudrate is 250000. This baudrate has less jitter and hence errors than the usual 115200 baud, but is less supported by drivers and host-environments.

Differences and additions to the already good Sprinter firmware:
================================================================

Look-ahead:
-----------

Marlin has look-ahead. While sprinter has to break and re-accelerate at each corner,
lookahead will only decelerate and accelerate to a velocity,
so that the change in vectorial velocity magnitude is less than the xy_jerk_velocity.
This is only possible, if some future moves are already processed, hence the name.
It leads to less over-deposition at corners, especially at flat angles.

Arc support:
------------

Slic3r can find curves that, although broken into segments, were ment to describe an arc.
Marlin is able to print those arcs. The advantage is the firmware can choose the resolution,
and can perform the arc with nearly constant velocity, resulting in a nice finish.
Also, less serial communication is needed.

Temperature Oversampling:
-------------------------

To reduce noise and make the PID-differential term more useful, 16 ADC conversion results are averaged.

AutoTemp:
---------

If your gcode contains a wide spread of extruder velocities, or you realtime change the building speed, the temperature should be changed accordingly.
Usually, higher speed requires higher temperature.
This can now be performed by the AutoTemp function
By calling M109 S<mintemp> B<maxtemp> F<factor> you enter the autotemp mode.

You can leave it by calling M109 without any F.
If active, the maximal extruder stepper rate of all buffered moves will be calculated, and named "maxerate" [steps/sec].
The wanted temperature then will be set to t=tempmin+factor*maxerate, while being limited between tempmin and tempmax.
If the target temperature is set manually or by gcode to a value less then tempmin, it will be kept without change.
Ideally, your gcode can be completely free of temperature controls, apart from a M109 S T F in the start.gcode, and a M109 S0 in the end.gcode.

EEPROM:
-------

If you know your PID values, the acceleration and max-velocities of your unique machine, you can set them, and finally store them in the EEPROM.
After each reboot, it will magically load them from EEPROM, independent what your Configuration.h says.

LCD Menu:
---------

If your hardware supports it, you can build yourself a LCD-CardReader+Click+encoder combination. It will enable you to realtime tune temperatures,
accelerations, velocities, flow rates, select and print files from the SD card, preheat, disable the steppers, and do other fancy stuff.
One working hardware is documented here: http://www.thingiverse.com/thing:12663
Also, with just a 20x4 or 16x2 display, useful data is shown.

SD card folders:
----------------

If you have an SD card reader attached to your controller, also folders work now. Listing the files in pronterface will show "/path/subpath/file.g".
You can write to file in a subfolder by specifying a similar text using small letters in the path.
Also, backup copies of various operating systems are hidden, as well as files not ending with ".g".

SD card folders:
----------------

If you place a file auto[0-9].g into the root of the sd card, it will be automatically executed if you boot the printer. The same file will be executed by selecting "Autostart" from the menu.
First *0 will be performed, than *1 and so on. That way, you can heat up or even print automatically without user interaction.

Endstop trigger reporting:
--------------------------

If an endstop is hit while moving towards the endstop, the location at which the firmware thinks that the endstop was triggered is outputed on the serial port.
This is useful, because the user gets a warning message.
However, also tools like QTMarlin can use this for finding acceptable combinations of velocity+acceleration.

Coding paradigm:
----------------

Not relevant from a user side, but Marlin was split into thematic junks, and has tried to partially enforced private variables.
This is intended to make it clearer, what interacts which what, and leads to a higher level of modularization.
We think that this is a useful prestep for porting this firmware to e.g. an ARM platform in the future.
A lot of RAM (with enabled LCD ~2200 bytes) was saved by storing char []="some message" in Program memory.
In the serial communication, a #define based level of abstraction was enforced, so that it is clear that
some transfer is information (usually beginning with "echo:"), an error "error:", or just normal protocol,
necessary for backwards compatibility.

Interrupt based temperature measurements:
-----------------------------------------

An interrupt is used to manage ADC conversions, and enforce checking for critical temperatures.
This leads to less blocking in the heater management routine.

Implemented G Codes:
====================

*  G0  -> G1
*  G1  - Coordinated Movement X Y Z E
*  G2  - CW ARC
*  G3  - CCW ARC
*  G4  - Dwell S<seconds> or P<milliseconds>
*  G10 - retract filament according to settings of M207
*  G11 - retract recover filament according to settings of M208
*  G28 - Home all Axis
*  G29 - Detailed Z-Probe, probes the bed at 3 points.  You must de at the home position for this to work correctly.
*  G30 - Single Z Probe, probes bed at current XY location.
*  G31 - Dock Z Probe sled (if enabled)
*  G32 - Undock Z Probe sled (if enabled)
*  G90 - Use Absolute Coordinates
*  G91 - Use Relative Coordinates
*  G92 - Set current position to cordinates given

M Codes
*  M0   - Unconditional stop - Wait for user to press a button on the LCD (Only if ULTRA_LCD is enabled)
*  M1   - Same as M0
*  M17  - Enable/Power all stepper motors
*  M18  - Disable all stepper motors; same as M84
*  M20  - List SD card
*  M21  - Init SD card
*  M22  - Release SD card
*  M23  - Select SD file (M23 filename.g)
*  M24  - Start/resume SD print
*  M25  - Pause SD print
*  M26  - Set SD position in bytes (M26 S12345)
*  M27  - Report SD print status
*  M28  - Start SD write (M28 filename.g)
*  M29  - Stop SD write
*  M30  - Delete file from SD (M30 filename.g)
*  M31  - Output time since last M109 or SD card start to serial
*  M32  - Select file and start SD print (Can be used when printing from SD card)
*  M42  - Change pin status via gcode Use M42 Px Sy to set pin x to value y, when omitting Px the onboard led will be used.
*  M80  - Turn on Power Supply
*  M81  - Turn off Power Supply
*  M82  - Set E codes absolute (default)
*  M83  - Set E codes relative while in Absolute Coordinates (G90) mode
*  M84  - Disable steppers until next move, or use S<seconds> to specify an inactivity timeout, after which the steppers will be disabled.  S0 to disable the timeout.
*  M85  - Set inactivity shutdown timer with parameter S<seconds>. To disable set zero (default)
*  M92  - Set axis_steps_per_unit - same syntax as G92
*  M104 - Set extruder target temp
*  M105 - Read current temp
*  M106 - Fan on
*  M107 - Fan off
*  M109 - Sxxx Wait for extruder current temp to reach target temp. Waits only when heating
*         Rxxx Wait for extruder current temp to reach target temp. Waits when heating and cooling
*  M112 - Emergency stop
*  M114 - Output current position to serial port
*  M115 - Capabilities string
*  M117 - display message
*  M119 - Output Endstop status to serial port
*  M126 - Solenoid Air Valve Open (BariCUDA support by jmil)
*  M127 - Solenoid Air Valve Closed (BariCUDA vent to atmospheric pressure by jmil)
*  M128 - EtoP Open (BariCUDA EtoP = electricity to air pressure transducer by jmil)
*  M129 - EtoP Closed (BariCUDA EtoP = electricity to air pressure transducer by jmil)
*  M140 - Set bed target temp
*  M190 - Sxxx Wait for bed current temp to reach target temp. Waits only when heating
*         Rxxx Wait for bed current temp to reach target temp. Waits when heating and cooling
*  M200 D<millimeters>- set filament diameter and set E axis units to cubic millimeters (use S0 to set back to millimeters).
*  M201 - Set max acceleration in units/s^2 for print moves (M201 X1000 Y1000)
*  M202 - Set max acceleration in units/s^2 for travel moves (M202 X1000 Y1000) Unused in Marlin!!
*  M203 - Set maximum feedrate that your machine can sustain (M203 X200 Y200 Z300 E10000) in mm/sec
*  M204 - Set default acceleration: S normal moves T filament only moves (M204 S3000 T7000) im mm/sec^2  also sets minimum segment time in ms (B20000) to prevent buffer underruns and M20 minimum feedrate
*  M205 -  advanced settings:  minimum travel speed S=while printing T=travel only,  B=minimum segment time X= maximum xy jerk, Z=maximum Z jerk, E=maximum E jerk
*  M206 - set additional homeing offset
*  M207 - set retract length S[positive mm] F[feedrate mm/min] Z[additional zlift/hop], stays in mm regardless of M200 setting
*  M208 - set recover=unretract length S[positive mm surplus to the M207 S*] F[feedrate mm/min]
*  M209 - S<1=true/0=false> enable automatic retract detect if the slicer did not support G10/11: every normal extrude-only move will be classified as retract depending on the direction.
*  M218 - set hotend offset (in mm): T<extruder_number> X<offset_on_X> Y<offset_on_Y>
*  M220 S<factor in percent>- set speed factor override percentage
*  M221 S<factor in percent>- set extrude factor override percentage
*  M240 - Trigger a camera to take a photograph
*  M280 - Position an RC Servo P<index> S<angle/microseconds>, ommit S to report back current angle
*  M300 - Play beepsound S<frequency Hz> P<duration ms>
*  M301 - Set PID parameters P I and D
*  M302 - Allow cold extrudes
*  M303 - PID relay autotune S<temperature> sets the target temperature. (default target temperature = 150C)
*  M304 - Set bed PID parameters P I and D
*  M400 - Finish all moves
*  M401 - Lower z-probe if present
*  M402 - Raise z-probe if present
*  M404 - N<dia in mm> Enter the nominal filament width (3mm, 1.75mm ) or will display nominal filament width without parameters
*  M405 - Turn on Filament Sensor extrusion control.  Optional D<delay in cm> to set delay in centimeters between sensor and extruder
*  M406 - Turn off Filament Sensor extrusion control
*  M407 - Displays measured filament diameter
*  M500 - stores paramters in EEPROM
*  M501 - reads parameters from EEPROM (if you need reset them after you changed them temporarily).
*  M502 - reverts to the default "factory settings".  You still need to store them in EEPROM afterwards if you want to.
*  M503 - print the current settings (from memory not from eeprom)
*  M540 - Use S[0|1] to enable or disable the stop SD card print on endstop hit (requires ABORT_ON_ENDSTOP_HIT_FEATURE_ENABLED)
*  M600 - Pause for filament change X[pos] Y[pos] Z[relative lift] E[initial retract] L[later retract distance for removal]
*  M907 - Set digital trimpot motor current using axis codes.
*  M908 - Control digital trimpot directly.
*  M350 - Set microstepping mode.
*  M351 - Toggle MS1 MS2 pins directly.
*  M928 - Start SD logging (M928 filename.g) - ended by M29
*  M999 - Restart after being stopped by error

Configuring and compilation:
============================

Install the latest non-beta arduino software IDE/toolset
   http://www.arduino.cc/en/Main/Software

Download the Marlin firmware
   https://github.com/MarlinFirmware/Marlin/tree/development
   
   For the latest development, or 

   For the latest stable release
   
   In both cases use the "Download Zip" button on the right.

For some spec. boards a spec. dir in the ArduinoAddons directory in the Marlin dir needs to be copied to the arduino environment. <arduino home>\hardware\

Start the arduino IDE.
Select Tools -> Board -> Arduino Mega 2560    or your microcontroller
Select the correct serial port in Tools ->Serial Port
Open Marlin.pde or .ino

Click the Verify/Compile button

Click the Upload button
If all goes well the firmware is uploading

That's ok.  Enjoy Silky Smooth Printing.

===============================================
Instructions for configuring Bed Auto Leveling
===============================================
There are two options for this feature. You may choose to use a servo mounted on the X carriage or you may use a sled that mounts on the X axis and can be docked when not in use.
See the section for each option below for specifics about installation and configuration. Also included are instructions that apply to both options.

Instructions for Both Options
-----------------------------

Uncomment the "ENABLE_AUTO_BED_LEVELING" define (commented by default)

The following options define the probing positions. These are good starting values.
I recommend to keep a better clearance from borders in the first run and then make the probes as close as possible to borders:

* \#define LEFT_PROBE_BED_POSITION 30
* \#define RIGHT_PROBE_BED_POSITION 140
* \#define BACK_PROBE_BED_POSITION 140
* \#define FRONT_PROBE_BED_POSITION 30

A few more options:

* \#define XY_TRAVEL_SPEED 6000

X and Y axis travel speed between probes, in mm/min.
Bear in mind that really fast moves may render step skipping. 6000 mm/min (100mm/s) is a good value.

* \#define Z_RAISE_BEFORE_PROBING 10
* \#define Z_RAISE_BETWEEN_PROBINGS 10

The Z axis is lifted when traveling to the first probe point by Z_RAISE_BEFORE_PROBING value
and then lifted when traveling from first to second and second to third point by Z_RAISE_BETWEEN_PROBINGS.
All values are in mm as usual.

Servo Option Notes
------------------
You will probably need a swivel Z-MIN endstop in the extruder. A rc servo do a great job.
Check the system working here: http://www.youtube.com/watch?v=3IKMeOYz-1Q (Enable English subtitles)
Teasing ;-) video: http://www.youtube.com/watch?v=x8eqSQNAyro

In order to get the servo working, you need to enable:

* \#define NUM_SERVOS 1 // Servo index starts with 0 for M280 command

* \#define SERVO_ENDSTOPS {-1, -1, 0} // Servo index for X, Y, Z. Disable with -1

* \#define SERVO_ENDSTOP_ANGLES {0,0, 0,0, 165,60} // X,Y,Z Axis Extend and Retract angles

The first define tells firmware how many servos you have.
The second tells what axis this servo will be attached to. In the example above, we have a servo in Z axis.
The third one tells the angle in 2 situations: Probing (165º) and resting (60º). Check this with command M280 P0 S{angle} (example: M280 P0 S60 moves the servo to 60º)

Next you need to define the Z endstop (probe) offset from hotend.
My preferred method:

* a) Make a small mark in the bed with a marker/felt-tip pen.
* b) Place the hotend tip as *exactly* as possible on the mark, touching the bed. Raise the hotend 0.1mm (a regular paper thickness) and zero all axis (G92 X0 Y0 Z0);
* d) Raise the hotend 10mm (or more) for probe clearance, lower the Z probe (Z-Endstop) with M401 and place it just on that mark by moving X, Y and Z;
* e) Lower the Z in 0.1mm steps, with the probe always touching the mark (it may be necessary to adjust X and Y as well) until you hear the "click" meaning the mechanical endstop was trigged. You can confirm with M119;
* f) Now you have the probe in the same place as your hotend tip was before. Perform a M114 and write down the values, for example: X:24.3 Y:-31.4 Z:5.1;
* g) You can raise the z probe with M402 command;
* h) Fill the defines bellow multiplying the values by "-1" (just change the signal)

* \#define X_PROBE_OFFSET_FROM_EXTRUDER -24.3
* \#define Y_PROBE_OFFSET_FROM_EXTRUDER 31.4
* \#define Z_PROBE_OFFSET_FROM_EXTRUDER -5.1

Sled Option Notes
-----------------
The sled option uses an electromagnet to attach and detach to/from the X carriage. See http://www.thingiverse.com/thing:396692 for more details on how to print and install this feature. It uses the same connections as the servo option.

To use the sled option, you must define two additional things in Configuration.h:

* \#define Z_PROBE_SLED
* \#define SLED_DOCKING_OFFSET 5

Uncomment the Z_PROBE_SLED to define to enable the sled (commented out by default).

Uncomment the SLED_DOCKING_OFFSET to set the extra distance the X axis must travel to dock the sled. This value can be found by moving the X axis to its maximum position then measure the distance to the right X end and subtract the width of the sled (23mm if you printed the sled from Thingiverse).

Next you need to define the Z endstop (probe) offset from hotend.
My preferred method:

* a) Home the X and Y axes.
* b) Move the X axis to about the center of the print bed. Make a mark on the print bed.
* c) Move the Y axis to the maximum position. Make another mark.
* d) Home the X axis and use a straight edge to make a line between the two points.
* e) Repeat (b)-(d) reversing the X and Y. When you are done you will have two lines on the print bed. We will use these to measure the offset for the Z probe endstop.
* f) Move the nozzle so that it is positioned on the center point of the two lines. You can use fine movement of 0.1mm to get it as close as possible. Note the position of X and Y.
* g) Zero the Z axis with the G92 Z0 command.
* h) Raise the Z axis about 20mmm.
* i) Use the G32 command to retrieve the sled.
* j) Now more the X and Y axis to the position recorded in (f).
* k) Lower the Z axis in 0.1mm steps until you hear the "click" meaning the mechanical endstop was trigged. You can confirm with the M119 command. Note the position of the Z axis.
* l) Make a mark on the print bed where the endstop lever has touched the print bed. Raise the Z-axis about 30mm to give yourself some room.
* m) Now measure the distance from the center point to the endstop impact site along the X and Y axis using the lines drawn previously.
* n) Fill in the values below. If the endstop mark is in front of the line running left-to-right, use positive values. If it is behind, use negative values. For the Z axis use the value from (k) and subtract 0.1mm.

For example, suppose you measured the endstop position and it was 20mm to the right of the line running front-to-back, 10mm toward the front of the line running left-to-right, and the value from (k) was 2.85. The values for the defines would be:

* \#define X_PROBE_OFFSET_FROM_EXTRUDER 20
* \#define Y_PROBE_OFFSET_FROM_EXTRUDER 10
* \#define Z_PROBE_OFFSET_FROM_EXTRUDER 2.75

That's it.. enjoy never having to calibrate your Z endstop neither leveling your bed by hand anymore ;-)

Filament Sensor
---------------
Supports the use of a real time filament diameter sensor that measures the diameter of the filament going into the extruder and then adjusts the extrusion rate to compensate for filament that does not match what is defined in the g-code.  The diameter can also be displayed on the LCD screen. This potentially eliminates the need to measure filament diameter when changing spools of filament. Gcode becomes independent of the filament diameter. Can also compensate for changing diameter.

For examples of these sensors, see: http://www.thingiverse.com/thing:454584, https://www.youmagine.com/designs/filament-diameter-sensor, http://diy3dprinting.blogspot.com/2014/01/diy-filament-diameter-sensor.html. Any sensor which produces a voltage equivalent to the diameter in mm (i.e. 1v = 1mm) can be used. This provides a very simple interface and may encourage more innovation in this area.

4 new Mcodes are defined to set relevant parameters: M404, M405, M406, M407 - see above.

 Implements a delay buffer to handle the transit delay between where the filament is measured and when it gets to the extruder.

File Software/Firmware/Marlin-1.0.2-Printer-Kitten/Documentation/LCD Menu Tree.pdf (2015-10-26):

# Marlin LCD Menu Tree

Main Menu | Tune Menu | Move Menu
Info screen | Main | Prepare
Tune | Speed | Move 10mm | Move Menu
Prepare | Nozzle | Move 1mm | Move axis
Control | Nozzle2 | Move 0.1mm | Move X
Pause print | Nozzle3 | | Move Y
Resume print | Bed | | Move Z
Stop print | Fan speed | Temperature Menu | Extruder
Print from SD | Flow | Control
Change SD card | Babystep X | Nozzle
No SD card | Babystep Y | Nozzle2
Init. SD card | Babystep Z | Nozzle3
| Change filament | Bed
| | Fan speed
| | Autotemp
| Prepare Menu | \002 Min
| Main | \002 Max | Preheat PLA
| Autostart | \002 Fact | Temperature
| Disable steppers | PID-P | Fan speed
| Auto home | PID-I | Nozzle
| Preheat PLA | PID-D | Bed
| Preheat ABS | PID-C | Store memory
| Cooldown | Preheat PLA conf
| Switch power off | Preheat ABS conf | Preheat ABS
Switch power on | Temperature
Move axis | Fan speed
| Motion Menu | Nozzle
| Control | Bed
Control Menu | Z Offset | Store memory
Main | Accel
Temperature | Vxy-jerk
Motion | Vz-jerk
LCD contrast | Ve-jerk
Retract | Vmax x
Store memory | Vmax y
Load memory | Vmax z
Restore failsafe | Vmax e
| Vmin
| VTrav min
SD Card Menu | Amax x
Main | Amax y
Refresh | Amax z
filenames | Amax e
| A-retract
| Xsteps/mm
| Ysteps/mm
| Zsteps/mm
| Esteps/mm
| Endstop abort

Retract Menu
Control
AutoRetr.
Retract mm
Retract F
Hop mm
UnRet +mm
UnRet F

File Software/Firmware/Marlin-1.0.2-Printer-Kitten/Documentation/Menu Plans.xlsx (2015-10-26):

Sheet: Menu Tree
Marlin LCD Menu Tree
 |  | Main Menu |  | Tune Menu |  | Move Menu
 | MSG_WATCH | Info screen | MSG_MAIN | Main | MSG_PREPARE | Prepare
 | MSG_TUNE | Tune | MSG_SPEED | Speed | MSG_MOVE_10MM | Move 10mm |  | Move Menu
 | MSG_PREPARE | Prepare | MSG_NOZZLE | Nozzle | MSG_MOVE_1MM | Move 1mm | MSG_MOVE_AXIS | Move axis
 | MSG_CONTROL | Control | MSG_NOZZLE1 | Nozzle2 | MSG_MOVE_01MM | Move 0.1mm | MSG_MOVE_X | Move X
 | MSG_PAUSE_PRINT | Pause print | MSG_NOZZLE2 | Nozzle3 |  |  | MSG_MOVE_Y | Move Y
 | MSG_RESUME_PRINT | Resume print | MSG_BED | Bed |  |  | MSG_MOVE_Z | Move Z
 | MSG_STOP_PRINT | Stop print | MSG_FAN_SPEED | Fan speed |  | Temperature Menu | MSG_MOVE_E | Extruder
 | MSG_CARD_MENU | Print from SD | MSG_FLOW | Flow | MSG_CONTROL | Control
 | MSG_CNG_SDCARD | Change SD card | MSG_BABYSTEP_X | Babystep X | MSG_NOZZLE | Nozzle
 | MSG_NO_CARD | No SD card | MSG_BABYSTEP_Y | Babystep Y | MSG_NOZZLE1 | Nozzle2
 | MSG_INIT_SDCARD | Init. SD card | MSG_BABYSTEP_Z | Babystep Z | MSG_NOZZLE2 | Nozzle3
 |  |  | MSG_FILAMENTCHANGE | Change filament | MSG_BED | Bed
 |  |  |  |  | MSG_FAN_SPEED | Fan speed
 |  |  |  |  | MSG_AUTOTEMP | Autotemp
 |  |  |  | Prepare Menu | MSG_MIN | \002 Min
 |  |  | MSG_MAIN | Main | MSG_MAX | \002 Max |  | Preheat PLA
 |  |  | MSG_AUTOSTART | Autostart | MSG_FACTOR | \002 Fact | MSG_TEMPERATURE | Temperature
 |  |  | MSG_DISABLE_STEPPERS | Disable steppers | MSG_PID_P | PID-P | MSG_FAN_SPEED | Fan speed
 |  |  | MSG_AUTO_HOME | Auto home | MSG_PID_I | PID-I | MSG_NOZZLE | Nozzle
 |  |  | MSG_PREHEAT_PLA | Preheat PLA | MSG_PID_D | PID-D | MSG_BED | Bed
 |  |  | MSG_PREHEAT_ABS | Preheat ABS | MSG_PID_C | PID-C | MSG_STORE_EPROM | Store memory
 |  |  | MSG_COOLDOWN | Cooldown | MSG_PREHEAT_PLA_SETTINGS | Preheat PLA conf
 |  |  | MSG_SWITCH_PS_OFF | Switch power off | MSG_PREHEAT_ABS_SETTINGS | Preheat ABS conf |  | Preheat ABS
 |  |  | MSG_SWITCH_PS_ON | Switch power on |  |  | MSG_TEMPERATURE | Temperature
 |  |  | MSG_MOVE_AXIS | Move axis |  |  | MSG_FAN_SPEED | Fan speed
 |  |  |  |  |  | Motion Menu | MSG_NOZZLE | Nozzle
 |  |  |  |  | MSG_CONTROL | Control | MSG_BED | Bed
 |  |  |  | Control Menu | MSG_ZPROBE_ZOFFSET | Z Offset | MSG_STORE_EPROM | Store memory
 |  |  | MSG_MAIN | Main | MSG_ACC | Accel
 |  |  | MSG_TEMPERATURE | Temperature | MSG_VXY_JERK | Vxy-jerk
 |  |  | MSG_MOTION | Motion | MSG_VZ_JERK | Vz-jerk
 |  |  | MSG_CONTRAST | LCD contrast | MSG_VE_JERK | Ve-jerk
 |  |  | MSG_RETRACT | Retract | MSG_VMAX MSG_X | Vmax x
 |  |  | MSG_STORE_EPROM | Store memory | MSG_VMAX MSG_Y | Vmax y
 |  |  | MSG_LOAD_EPROM | Load memory | MSG_VMAX MSG_Z | Vmax z
 |  |  | MSG_RESTORE_FAILSAFE | Restore failsafe | MSG_VMAX MSG_E | Vmax e
 |  |  |  |  | MSG_VMIN | Vmin
 |  |  |  |  | MSG_VTRAV_MIN | VTrav min
 |  |  |  | SD Card Menu | MSG_AMAX MSG_X | Amax x
 |  |  | MSG_MAIN | Main | MSG_AMAX MSG_Y | Amax y
 |  |  | MSG_REFRESH | Refresh | MSG_AMAX MSG_Z | Amax z
 |  |  | filenames | filenames | MSG_AMAX MSG_E | Amax e
 |  |  |  |  | MSG_A_RETRACT | A-retract
 |  |  |  |  | MSG_XSTEPS | Xsteps/mm
 |  |  |  |  | MSG_YSTEPS | Ysteps/mm
 |  |  |  |  | MSG_ZSTEPS | Zsteps/mm
 |  |  |  |  | MSG_ESTEPS | Esteps/mm
 |  |  |  |  | MSG_ENDSTOP_ABORT | Endstop abort
 |  |  |  |  |  | Retract Menu
 |  |  |  |  | MSG_CONTROL | Control
 |  |  |  |  | MSG_AUTORETRACT | AutoRetr.
 |  |  |  |  | MSG_CONTROL_RETRACT | Retract mm
 |  |  |  |  | MSG_CONTROL_RETRACTF | Retract F
 |  |  |  |  | MSG_CONTROL_RETRACT_ZLIFT | Hop mm
 |  |  |  |  | MSG_CONTROL_RETRACT_RECOVER | UnRet +mm
 |  |  |  |  | MSG_CONTROL_RETRACT_RECOVERF | UnRet F

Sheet: Language File
Paste the #defines from language.h here, for the language you want a menu-plan of. Make sure to only paste one language, and that only the first column is changed! Formulas in B and C pull the text from the define.
#define WELCOME_MSG MACHINE_NAME " ready." | WELCOME_MSG MACHINE_NAME | ready.
#define MSG_SD_INSERTED "Card inserted" | MSG_SD_INSERTED | Card inserted
#define MSG_SD_REMOVED "Card removed" | MSG_SD_REMOVED | Card removed
#define MSG_MAIN "Main" | MSG_MAIN | Main
#define MSG_AUTOSTART "Autostart" | MSG_AUTOSTART | Autostart
#define MSG_DISABLE_STEPPERS "Disable steppers" | MSG_DISABLE_STEPPERS | Disable steppers
#define MSG_AUTO_HOME "Auto home" | MSG_AUTO_HOME | Auto home
#define MSG_SET_ORIGIN "Set origin" | MSG_SET_ORIGIN | Set origin
#define MSG_PREHEAT_PLA "Preheat PLA" | MSG_PREHEAT_PLA | Preheat PLA
#define MSG_PREHEAT_PLA_SETTINGS "Preheat PLA conf" | MSG_PREHEAT_PLA_SETTINGS | Preheat PLA conf
#define MSG_PREHEAT_ABS "Preheat ABS" | MSG_PREHEAT_ABS | Preheat ABS
#define MSG_PREHEAT_ABS_SETTINGS "Preheat ABS conf" | MSG_PREHEAT_ABS_SETTINGS | Preheat ABS conf
#define MSG_COOLDOWN "Cooldown" | MSG_COOLDOWN | Cooldown
#define MSG_SWITCH_PS_ON "Switch power on" | MSG_SWITCH_PS_ON | Switch power on
#define MSG_SWITCH_PS_OFF "Switch power off" | MSG_SWITCH_PS_OFF | Switch power off
#define MSG_EXTRUDE "Extrude" | MSG_EXTRUDE | Extrude
#define MSG_RETRACT "Retract" | MSG_RETRACT | Retract
#define MSG_MOVE_AXIS "Move axis" | MSG_MOVE_AXIS | Move axis
#define MSG_MOVE_X "Move X" | MSG_MOVE_X | Move X
#define MSG_MOVE_Y "Move Y" | MSG_MOVE_Y | Move Y
#define MSG_MOVE_Z "Move Z" | MSG_MOVE_Z | Move Z
#define MSG_MOVE_E "Extruder" | MSG_MOVE_E | Extruder
#define MSG_MOVE_01MM "Move 0.1mm" | MSG_MOVE_01MM | Move 0.1mm
#define MSG_MOVE_1MM "Move 1mm" | MSG_MOVE_1MM | Move 1mm
#define MSG_MOVE_10MM "Move 10mm" | MSG_MOVE_10MM | Move 10mm
#define MSG_SPEED "Speed" | MSG_SPEED | Speed
#define MSG_NOZZLE "Nozzle" | MSG_NOZZLE | Nozzle
#define MSG_NOZZLE1 "Nozzle2" | MSG_NOZZLE1 | Nozzle2
#define MSG_NOZZLE2 "Nozzle3" | MSG_NOZZLE2 | Nozzle3
#define MSG_BED "Bed" | MSG_BED | Bed
#define MSG_FAN_SPEED "Fan speed" | MSG_FAN_SPEED | Fan speed
#define MSG_FLOW "Flow" | MSG_FLOW | Flow
#define MSG_CONTROL "Control" | MSG_CONTROL | Control
#define MSG_MIN " \002 Min" | MSG_MIN | \002 Min
#define MSG_MAX " \002 Max" | MSG_MAX | \002 Max
#define MSG_FACTOR " \002 Fact" | MSG_FACTOR | \002 Fact
#define MSG_AUTOTEMP "Autotemp" | MSG_AUTOTEMP | Autotemp
#define MSG_ON "On " | MSG_ON | On
#define MSG_OFF "Off" | MSG_OFF | Off
#define MSG_PID_P "PID-P" | MSG_PID_P | PID-P
#define MSG_PID_I "PID-I" | MSG_PID_I | PID-I
#define MSG_PID_D "PID-D" | MSG_PID_D | PID-D
#define MSG_PID_C "PID-C" | MSG_PID_C | PID-C
#define MSG_ACC "Accel" | MSG_ACC | Accel
#define MSG_VXY_JERK "Vxy-jerk" | MSG_VXY_JERK | Vxy-jerk
#define MSG_VZ_JERK "Vz-jerk" | MSG_VZ_JERK | Vz-jerk
#define MSG_VE_JERK "Ve-jerk" | MSG_VE_JERK | Ve-jerk
#define MSG_VMAX "Vmax " | MSG_VMAX | Vmax
#define MSG_X "x" | MSG_X | x
#define MSG_Y "y" | MSG_Y | y
#define MSG_Z "z" | MSG_Z | z
#define MSG_E "e" | MSG_E | e
#define MSG_VMIN "Vmin" | MSG_VMIN | Vmin
#define MSG_VTRAV_MIN "VTrav min" | MSG_VTRAV_MIN | VTrav min
#define MSG_AMAX "Amax " | MSG_AMAX | Amax
#define MSG_A_RETRACT "A-retract" | MSG_A_RETRACT | A-retract
#define MSG_XSTEPS "Xsteps/mm" | MSG_XSTEPS | Xsteps/mm
#define MSG_YSTEPS "Ysteps/mm" | MSG_YSTEPS | Ysteps/mm
#define MSG_ZSTEPS "Zsteps/mm" | MSG_ZSTEPS | Zsteps/mm
#define MSG_ESTEPS "Esteps/mm" | MSG_ESTEPS | Esteps/mm
#define MSG_RECTRACT "Rectract" | MSG_RECTRACT | Rectract
#define MSG_TEMPERATURE "Temperature" | MSG_TEMPERATURE | Temperature
#define MSG_MOTION "Motion" | MSG_MOTION | Motion
#define MSG_CONTRAST "LCD contrast" | MSG_CONTRAST | LCD contrast
#define MSG_STORE_EPROM "Store memory" | MSG_STORE_EPROM | Store memory
#define MSG_LOAD_EPROM "Load memory" | MSG_LOAD_EPROM | Load memory
#define MSG_RESTORE_FAILSAFE "Restore failsafe" | MSG_RESTORE_FAILSAFE | Restore failsafe
#define MSG_REFRESH "Refresh" | MSG_REFRESH | Refresh
#define MSG_WATCH "Info screen" | MSG_WATCH | Info screen
#define MSG_PREPARE "Prepare" | MSG_PREPARE | Prepare
#define MSG_TUNE "Tune" | MSG_TUNE | Tune
#define MSG_PAUSE_PRINT "Pause print" | MSG_PAUSE_PRINT | Pause print
#define MSG_RESUME_PRINT "Resume print" | MSG_RESUME_PRINT | Resume print
#define MSG_STOP_PRINT "Stop print" | MSG_STOP_PRINT | Stop print
#define MSG_CARD_MENU "Print from SD" | MSG_CARD_MENU | Print from SD
#define MSG_NO_CARD "No SD card" | MSG_NO_CARD | No SD card
#define MSG_DWELL "Sleep..." | MSG_DWELL | Sleep...
#define MSG_USERWAIT "Wait for user..." | MSG_USERWAIT | Wait for user...
#define MSG_RESUMING "Resuming print" | MSG_RESUMING | Resuming print
#define MSG_NO_MOVE "No move." | MSG_NO_MOVE | No move.
#define MSG_KILLED "KILLED. " | MSG_KILLED | KILLED.
#define MSG_STOPPED "STOPPED. " | MSG_STOPPED | STOPPED.
#define MSG_CONTROL_RETRACT "Retract mm" | MSG_CONTROL_RETRACT | Retract mm
#define MSG_CONTROL_RETRACTF "Retract F" | MSG_CONTROL_RETRACTF | Retract F
#define MSG_CONTROL_RETRACT_ZLIFT "Hop mm" | MSG_CONTROL_RETRACT_ZLIFT | Hop mm
#define MSG_CONTROL_RETRACT_RECOVER "UnRet +mm" | MSG_CONTROL_RETRACT_RECOVER | UnRet +mm
#define MSG_CONTROL_RETRACT_RECOVERF "UnRet F" | MSG_CONTROL_RETRACT_RECOVERF | UnRet F
#define MSG_AUTORETRACT "AutoRetr." | MSG_AUTORETRACT | AutoRetr.
#define MSG_FILAMENTCHANGE "Change filament" | MSG_FILAMENTCHANGE | Change filament
#define MSG_INIT_SDCARD "Init. SD card" | MSG_INIT_SDCARD | Init. SD card
#define MSG_CNG_SDCARD "Change SD card" | MSG_CNG_SDCARD | Change SD card
#define MSG_ZPROBE_OUT "Z probe out. bed" | MSG_ZPROBE_OUT | Z probe out. bed
#define MSG_POSITION_UNKNOWN "Home X/Y before Z" | MSG_POSITION_UNKNOWN | Home X/Y before Z
#define MSG_ZPROBE_ZOFFSET "Z Offset" | MSG_ZPROBE_ZOFFSET | Z Offset
#define MSG_BABYSTEP_X "Babystep X" | MSG_BABYSTEP_X | Babystep X
#define MSG_BABYSTEP_Y "Babystep Y" | MSG_BABYSTEP_Y | Babystep Y
#define MSG_BABYSTEP_Z "Babystep Z" | MSG_BABYSTEP_Z | Babystep Z
#define MSG_ENDSTOP_ABORT "Endstop abort" | MSG_ENDSTOP_ABORT | Endstop abort
 | #VALUE! | #VALUE!
// Serial Console Messages | #VALUE! | #VALUE!
 | #VALUE! | #VALUE!
#define MSG_Enqueing "enqueing \"" | MSG_Enqueing | enqueing \"
#define MSG_POWERUP "PowerUp" | MSG_POWERUP | PowerUp
#define MSG_EXTERNAL_RESET " External Reset" | MSG_EXTERNAL_RESET | External Reset
#define MSG_BROWNOUT_RESET " Brown out Reset" | MSG_BROWNOUT_RESET | Brown out Reset
#define MSG_WATCHDOG_RESET " Watchdog Reset" | MSG_WATCHDOG_RESET | Watchdog Reset
#define MSG_SOFTWARE_RESET " Software Reset" | MSG_SOFTWARE_RESET | Software Reset
#define MSG_AUTHOR " | Author: " | MSG_AUTHOR | | Author:
#define MSG_CONFIGURATION_VER " Last Updated: " | MSG_CONFIGURATION_VER | Last Updated:
#define MSG_FREE_MEMORY " Free Memory: " | MSG_FREE_MEMORY | Free Memory:
#define MSG_PLANNER_BUFFER_BYTES " PlannerBufferBytes: " | MSG_PLANNER_BUFFER_BYTES | PlannerBufferBytes:
#define MSG_OK "ok" | MSG_OK | ok
#define MSG_FILE_SAVED "Done saving file." | MSG_FILE_SAVED | Done saving file.
#define MSG_ERR_LINE_NO "Line Number is not Last Line Number+1, Last Line: " | MSG_ERR_LINE_NO | Line Number is not Last Line Number+1, Last Line:
#define MSG_ERR_CHECKSUM_MISMATCH "checksum mismatch, Last Line: " | MSG_ERR_CHECKSUM_MISMATCH | checksum mismatch, Last Line:
#define MSG_ERR_NO_CHECKSUM "No Checksum with line number, Last Line: " | MSG_ERR_NO_CHECKSUM | No Checksum with line number, Last Line:
#define MSG_ERR_NO_LINENUMBER_WITH_CHECKSUM "No Line Number with checksum, Last Line: " | MSG_ERR_NO_LINENUMBER_WITH_CHECKSUM | No Line Number with checksum, Last Line:
#define MSG_FILE_PRINTED "Done printing file" | MSG_FILE_PRINTED | Done printing file
#define MSG_BEGIN_FILE_LIST "Begin file list" | MSG_BEGIN_FILE_LIST | Begin file list
#define MSG_END_FILE_LIST "End file list" | MSG_END_FILE_LIST | End file list
#define MSG_M104_INVALID_EXTRUDER "M104 Invalid extruder " | MSG_M104_INVALID_EXTRUDER | M104 Invalid extruder
#define MSG_M105_INVALID_EXTRUDER "M105 Invalid extruder " | MSG_M105_INVALID_EXTRUDER | M105 Invalid extruder
#define MSG_M200_INVALID_EXTRUDER "M200 Invalid extruder " | MSG_M200_INVALID_EXTRUDER | M200 Invalid extruder
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

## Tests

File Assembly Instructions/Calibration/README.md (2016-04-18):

# Calibration

## Bed level and Z-axis offset calibration

Run the gcode file [BedLevel_ZOffset.gcode](https://github.com/woolfepr/Printer-Kitten/blob/master/Assembly%20Instructions/Calibration/BedLevel_ZOffset.gcode) Copy it to the SD card, put the SD card in the printer. On the bottom of the main menu on the display it should say print from SD, navigate to the file run it.

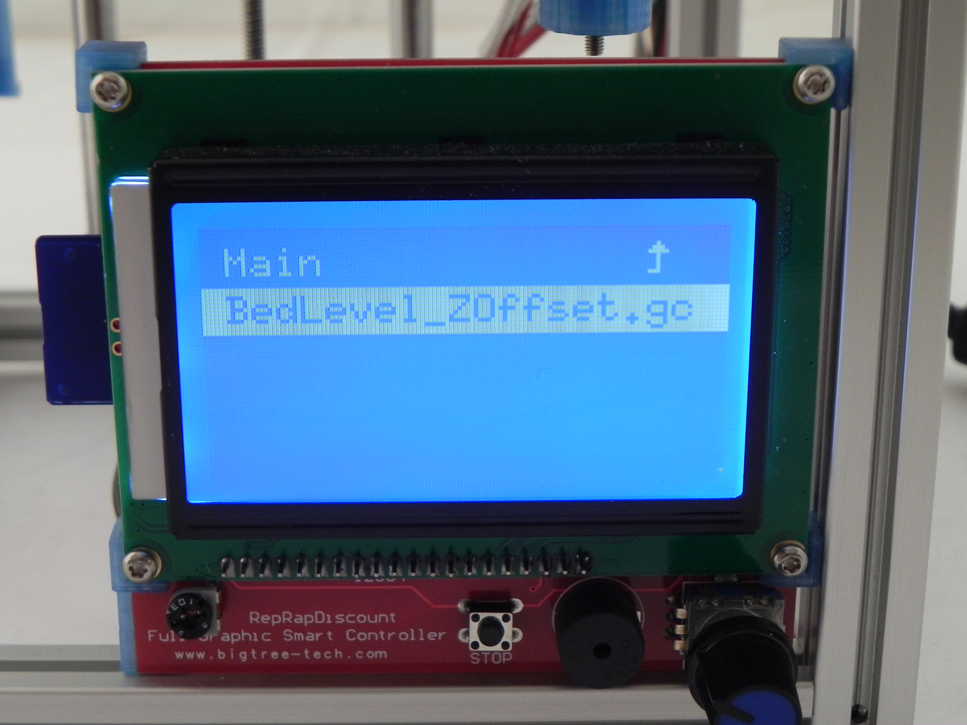
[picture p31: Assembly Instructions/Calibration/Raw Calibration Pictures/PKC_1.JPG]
Calibration Picture


After the Z-Axis has come to rest move the print head so the nozzle is above the left rear adjustment screw.

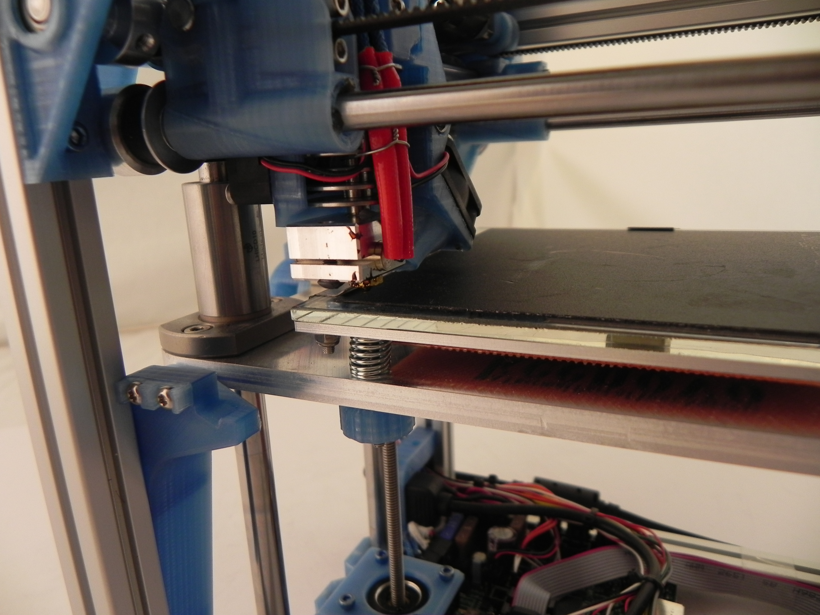
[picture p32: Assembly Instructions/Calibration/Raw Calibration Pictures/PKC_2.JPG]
Calibration Picture


Using about a 1"x 3" piece of standard printer paper (≈0.1mm thick) as a feeler gauge between the nozzle and build plate, turn the bed adjustment knob to move the bed up towards the nozzle. Move the bed up until as you move the piece of paper in and out you just start feeling resistance and the piece of paper buckles as you push it in.

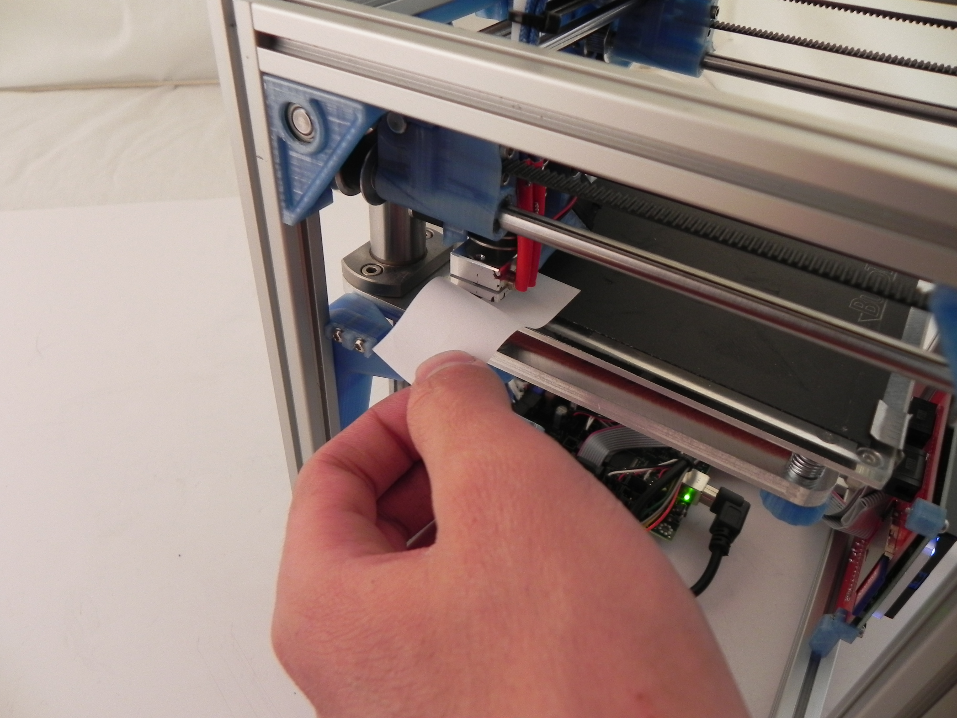
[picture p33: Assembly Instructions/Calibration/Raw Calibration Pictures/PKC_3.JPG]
Calibration Picture


Repeat the previous step for the front left and then front right. (note: the nozzle will not be able to move all the way right to go over the font right adjustment screw. Just move it as far right as it goes)

## [Load filament and perform first print](https://github.com/woolfepr/Printer-Kitten/tree/master/Assembly%20Instructions/First%20Print)

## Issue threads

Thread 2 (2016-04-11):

X axis and Y axis idler

hosemn, 2016-04-11:
In the "X axis idler" and "Y axis idler" sections, it mentions using the "shorter bolt from bag 8" and "longer bolt from bag 8," respectively.

...I didn't notice any difference in the lengths of the bolts provided in bag 8. What's going on here?
- Kit has been changed and documentation has not caught up
- There _was_ a difference, and I just happened to luck out and put the right ones on the right places
- There _was_ a difference, and I may have put the wrong things in the wrong places, putting myself, my home, and my loved ones in peril

My idlers are stable, don't float, and spin freely, so I assume everything is alright, but I wanted to make sure there's nothing that needs to be updated in the documentation.

woolfepr, 2016-04-12:
The threaded part of the shoulder bolts is the same length, but the shoulders should be different lengths. The shoulder and overall length of the bolt for the Y axis idler should be 4mm longer. If both of the idlers screwed in properly and don't float it sounds like you were sent the correct parts and assembled them correctly.

Closed 2016-12-27.

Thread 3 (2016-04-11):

Belt clamps 1 and 3 are hard to distinguish

hosemn, 2016-04-11:
When I was assembling my kit this weekend, it was very hard to distinguish clamps 1 and 3 from each other. Clamp piece 2 has a very distinct shape and size, making it easy to set apart from the other two, but I had to look *really* closely to distinguish 1 and 3 from each other. Even though 3 is supposed to have a clearance hole, the first one I picked up from my pile had enough extra material in the hole to make it almost seem threaded, so I had to really do a lot of sleuthing to come to what I expect was the correct conclusion.

Clamp piece 3 is slightly shorter than clamp piece 1, correct? Perhaps we should also include that in the description?

Should you also consider making a cosmetic change to the design of the pieces, so they are easier to distinguish? Like, maybe add a cross-hatch pattern to one side of clamp 1 or 3, or make the existing alignment groove only run halfway down the length of the part? That way there would be a more stark difference between 1 and 3, so builders could more easily distinguish between them.

woolfepr, 2016-04-12:
Thank for the good suggestions. Clamp 1 is longer than clamp 3. That is definitely an easier way to tell them apart than looking for which one has a threaded hole. I'll look into making some cosmetic changes to the parts, but at the very least will update the instructions to say clamp 1 is longer.

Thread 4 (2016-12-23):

cad files for aluminum plates?

bmarks-mylo, 2016-12-23:
Can you add the cad/dxf files for the aluminum plates please.

woolfepr, 2016-12-27:
Solid model files added

bmarks-mylo, 2016-12-27:
Thanks!

Closed 2016-12-27.

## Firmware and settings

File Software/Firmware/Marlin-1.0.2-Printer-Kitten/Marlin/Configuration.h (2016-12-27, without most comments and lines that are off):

#define CONFIGURATION_H
#include "boards.h"
#define STRING_VERSION_CONFIG_H __DATE__ " " __TIME__ // build date and time
#define STRING_CONFIG_H_AUTHOR "(none, default config)" // Who made the changes.
#define SERIAL_PORT 0
#define BAUDRATE 115200
#define MOTHERBOARD 302
#define CUSTOM_MENDEL_NAME "Kitten"
#define EXTRUDERS 1
#define POWER_SUPPLY 1
#define TEMP_SENSOR_0 5
#define TEMP_SENSOR_1 0
#define TEMP_SENSOR_2 0
#define TEMP_SENSOR_BED 60
#define MAX_REDUNDANT_TEMP_SENSOR_DIFF 10
#define TEMP_RESIDENCY_TIME 5  // (seconds)
#define TEMP_HYSTERESIS 4       // (degC) range of +/- temperatures considered "close" to the target one
#define TEMP_WINDOW     1       // (degC) Window around target to start the residency timer x degC early.
#define HEATER_0_MINTEMP 5
#define HEATER_1_MINTEMP 5
#define HEATER_2_MINTEMP 5
#define BED_MINTEMP 5
#define HEATER_0_MAXTEMP 300
#define HEATER_1_MAXTEMP 275
#define HEATER_2_MAXTEMP 275
#define BED_MAXTEMP 150
#define PIDTEMP
#define BANG_MAX 255 // limits current to nozzle while in bang-bang mode; 255=full current
#define PID_MAX BANG_MAX // limits current to nozzle while PID is active (see PID_FUNCTIONAL_RANGE below); 255=full current
  #define PID_FUNCTIONAL_RANGE 10 // If the temperature difference between the target temperature and the actual temperature
  #define PID_INTEGRAL_DRIVE_MAX PID_MAX  //limit for the integral term
  #define K1 0.95 //smoothing factor within the PID
  #define PID_dT ((OVERSAMPLENR * 10.0)/(F_CPU / 64.0 / 256.0)) //sampling period of the temperature routine
    #define  DEFAULT_Kp 29.71
    #define  DEFAULT_Ki 2.30
    #define  DEFAULT_Kd 96.12
#define PIDTEMPBED
#define MAX_BED_POWER 255 // limits duty cycle to bed; 255=full current
    #define  DEFAULT_bedKp 98.36
    #define  DEFAULT_bedKi 19.06
    #define  DEFAULT_bedKd 126.91
#define PREVENT_DANGEROUS_EXTRUDE
#define PREVENT_LENGTHY_EXTRUDE
#define EXTRUDE_MINTEMP 170
#define EXTRUDE_MAXLENGTH (X_MAX_LENGTH+Y_MAX_LENGTH) //prevent extrusion of very large distances.
#define THERMAL_RUNAWAY_PROTECTION_START_PERIOD 20
#define THERMAL_RUNAWAY_PROTECTION_PERIOD 60 //in seconds
#define THERMAL_RUNAWAY_PROTECTION_HYSTERESIS 15 // in degree Celsius
#define ENDSTOPPULLUPS // Comment this out (using // at the start of the line) to disable the endstop pullup resistors
  #define ENDSTOPPULLUP_XMAX
  #define ENDSTOPPULLUP_YMAX
  #define ENDSTOPPULLUP_ZMAX
  #define ENDSTOPPULLUP_XMIN
  #define ENDSTOPPULLUP_YMIN
  #define ENDSTOPPULLUP_ZMIN
const bool X_MIN_ENDSTOP_INVERTING = true; // set to true to invert the logic of the endstop.
const bool Y_MIN_ENDSTOP_INVERTING = true; // set to true to invert the logic of the endstop.
const bool Z_MIN_ENDSTOP_INVERTING = true; // set to true to invert the logic of the endstop.
const bool X_MAX_ENDSTOP_INVERTING = true; // set to true to invert the logic of the endstop.
const bool Y_MAX_ENDSTOP_INVERTING = true; // set to true to invert the logic of the endstop.
const bool Z_MAX_ENDSTOP_INVERTING = true; // set to true to invert the logic of the endstop.
#if defined(COREXY) && !defined(DISABLE_MAX_ENDSTOPS)
  #define DISABLE_MAX_ENDSTOPS
#endif
#define X_ENABLE_ON 0
#define Y_ENABLE_ON 0
#define Z_ENABLE_ON 0
#define E_ENABLE_ON 0 // For all extruders
#define DISABLE_X false
#define DISABLE_Y false
#define DISABLE_Z false
#define DISABLE_E false // For all extruders
#define DISABLE_INACTIVE_EXTRUDER true //disable only inactive extruders and keep active extruder enabled
#define INVERT_X_DIR true    // for Mendel set to false, for Orca set to true initially false
#define INVERT_Y_DIR false    // for Mendel set to true, for Orca set to false initially true
#define INVERT_Z_DIR false     // for Mendel set to false, for Orca set to true
#define INVERT_E0_DIR true   // for direct drive extruder v9 set to true, for geared extruder set to false
#define INVERT_E1_DIR false    // for direct drive extruder v9 set to true, for geared extruder set to false
#define INVERT_E2_DIR false   // for direct drive extruder v9 set to true, for geared extruder set to false
#define X_HOME_DIR 1
#define Y_HOME_DIR 1
#define Z_HOME_DIR -1
#define min_software_endstops true // If true, axis won't move to coordinates less than HOME_POS.
#define max_software_endstops true  // If true, axis won't move to coordinates greater than the defined lengths below.
#define X_MAX_POS 100
#define X_MIN_POS 0
#define Y_MAX_POS 100
#define Y_MIN_POS 0
#define Z_MAX_POS 100
#define Z_MIN_POS 0
#define X_MAX_LENGTH (X_MAX_POS - X_MIN_POS)
#define Y_MAX_LENGTH (Y_MAX_POS - Y_MIN_POS)
#define Z_MAX_LENGTH (Z_MAX_POS - Z_MIN_POS)
#define Z_PROBE_REPEATABILITY_TEST  // If not commented out, Z-Probe Repeatability test will be included if Auto Bed Leveling is Enabled.
#define MANUAL_X_HOME_POS 0
#define MANUAL_Y_HOME_POS 0
#define MANUAL_Z_HOME_POS 0
#define NUM_AXIS 4 // The axis order in all axis related arrays is X, Y, Z, E
#define HOMING_FEEDRATE {25*60, 25*60, 8*60, 0}  // set the homing speeds (mm/min)
#define DEFAULT_AXIS_STEPS_PER_UNIT   {100,100,1600,430}  // 430 for Bondtech 1.75mm, 500 for Bondtech 2.85mm(3mm), 404 for Titan 2.85mm(3mm)
#define DEFAULT_MAX_FEEDRATE          {150, 150, 15, 55}    // (mm/sec)  55 for Bondtech, 45 for Titan
#define DEFAULT_MAX_ACCELERATION      {3500,3500,200,3000}    // X, Y, Z, E maximum start speed for accelerated moves. E default values are good for Skeinforge 40+, for older versions raise them a lot.
#define DEFAULT_ACCELERATION          3000    // X, Y, Z and E max acceleration in mm/s^2 for printing moves
#define DEFAULT_RETRACT_ACCELERATION  3000   // X, Y, Z and E max acceleration in mm/s^2 for retracts
#define DEFAULT_XYJERK                12.0    // (mm/sec)
#define DEFAULT_ZJERK                 0.4     // (mm/sec)
#define DEFAULT_EJERK                 5.0    // (mm/sec)
#define CUSTOM_M_CODES
  #define CUSTOM_M_CODE_SET_Z_PROBE_OFFSET 851
  #define Z_PROBE_OFFSET_RANGE_MIN -15
  #define Z_PROBE_OFFSET_RANGE_MAX -5
#define PLA_PREHEAT_HOTEND_TEMP 210
#define PLA_PREHEAT_HPB_TEMP 0
#define PLA_PREHEAT_FAN_SPEED 101   // Insert Value between 0 and 255
#define ABS_PREHEAT_HOTEND_TEMP 240
#define ABS_PREHEAT_HPB_TEMP 100
#define ABS_PREHEAT_FAN_SPEED 101   // Insert Value between 0 and 255
#define REPRAP_DISCOUNT_FULL_GRAPHIC_SMART_CONTROLLER
 #define DOGLCD
 #define U8GLIB_ST7920
 #define REPRAP_DISCOUNT_SMART_CONTROLLER
 #define ULTIPANEL
 #define NEWPANEL
  #define SDSUPPORT
  #define ULTRA_LCD
    #define LCD_WIDTH 20
    #define LCD_HEIGHT 5
    #define DEFAULT_LCD_CONTRAST 32
#define SOFT_PWM_SCALE 0
#define FILAMENT_SENSOR_EXTRUDER_NUM	0  //The number of the extruder that has the filament sensor (0,1,2)
#define MEASUREMENT_DELAY_CM			14  //measurement delay in cm.  This is the distance from filament sensor to middle of barrel
#define DEFAULT_NOMINAL_FILAMENT_DIA  3.0  //Enter the diameter (in mm) of the filament generally used (3.0 mm or 1.75 mm) - this is then used in the slicer software.  Used for sensor reading validation
#define MEASURED_UPPER_LIMIT          3.30  //upper limit factor used for sensor reading validation in mm
#define MEASURED_LOWER_LIMIT          1.90  //lower limit factor for sensor reading validation in mm
#define MAX_MEASUREMENT_DELAY			20  //delay buffer size in bytes (1 byte = 1cm)- limits maximum measurement delay allowable (must be larger than MEASUREMENT_DELAY_CM  and lower number saves RAM)
#define DEFAULT_MEASURED_FILAMENT_DIA  DEFAULT_NOMINAL_FILAMENT_DIA  //set measured to nominal initially
#include "Configuration_adv.h"
#include "thermistortables.h"

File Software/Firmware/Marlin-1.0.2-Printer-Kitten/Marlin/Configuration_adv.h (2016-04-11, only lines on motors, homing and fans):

#define CONTROLLERFAN_PIN -1 //Pin used for the fan to cool controller (-1 to disable)
#define EXTRUDER_0_AUTO_FAN_PIN   -1
#define EXTRUDER_1_AUTO_FAN_PIN   -1
#define EXTRUDER_2_AUTO_FAN_PIN   -1
#define ENDSTOPS_ONLY_FOR_HOMING // If defined the endstops will only be used for homing
#define X_HOME_RETRACT_MM 2
#define Y_HOME_RETRACT_MM 2
#define Z_HOME_RETRACT_MM .4
#define MICROSTEP1 LOW,LOW
#define MICROSTEP2 HIGH,LOW
#define MICROSTEP4 LOW,HIGH
#define MICROSTEP8 HIGH,HIGH
#define MICROSTEP16 HIGH,HIGH
#define MICROSTEP_MODES {16,16,16,16,16} // [1,2,4,8,16]
#define DIGIPOT_MOTOR_CURRENT {135,135,135,135,135} // Values 0-255 (RAMBO 135 = ~0.75A, 185 = ~1A)
#define DIGIPOT_I2C_MOTOR_CURRENTS {1.0, 1.0, 1.0, 1.0, 1.0, 1.0, 1.0, 1.0}

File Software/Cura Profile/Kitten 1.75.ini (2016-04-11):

[profile]
layer_height = .16
wall_thickness = .8
retraction_enable = True
solid_layer_thickness = .64
fill_density = 24
nozzle_size = .4
print_speed = 30
print_temperature = 215
print_temperature2 = 0
print_temperature3 = 0
print_temperature4 = 0
print_temperature5 = 0
print_bed_temperature = 40
support = None
platform_adhesion = None
support_dual_extrusion = Both
wipe_tower = False
wipe_tower_volume = 15
ooze_shield = False
filament_diameter = 1.75
filament_diameter2 = 0
filament_diameter3 = 0
filament_diameter4 = 0
filament_diameter5 = 0
filament_flow = 100.0
retraction_speed = 100
retraction_amount = 10
retraction_dual_amount = 16.5
retraction_min_travel = 1.5
retraction_combing = All
retraction_minimal_extrusion = 0.02
retraction_hop = .3
bottom_thickness = 0.24
layer0_width_factor = 100
object_sink = 0
overlap_dual = 0.15
travel_speed = 500
bottom_layer_speed = 10
infill_speed = 0.0
solidarea_speed = 0.0
inset0_speed = 0.0
insetx_speed = 0.0
cool_min_layer_time = 15
fan_enabled = True
skirt_line_count = 0
skirt_gap = 3.0
skirt_minimal_length = 100
fan_full_height = 3
fan_speed = 100
fan_speed_max = 100
cool_min_feedrate = 10
cool_head_lift = False
solid_top = True
solid_bottom = True
fill_overlap = 15
support_type = Lines
support_angle = 60
support_fill_rate = 15
support_xy_distance = 0.7
support_z_distance = 0.15
spiralize = False
simple_mode = False
brim_line_count = 12
raft_margin = 5.0
raft_line_spacing = 3.0
raft_base_thickness = 0.3
raft_base_linewidth = 1.0
raft_interface_thickness = 0.27
raft_interface_linewidth = 0.4
raft_airgap_all = 0.0
raft_airgap = 0.22
raft_surface_layers = 2
raft_surface_thickness = 0.27
raft_surface_linewidth = 0.4
fix_horrible_union_all_type_a = True
fix_horrible_union_all_type_b = False
fix_horrible_use_open_bits = False
fix_horrible_extensive_stitching = False
plugin_config = (lp1
	(dp2
	S'params'
	p3
	(dp4
	S'dummy'
	p5
	V
	sS'retractSpeed'
	p6
	V18000
	p7
	sS'retractLen'
	p8
	V5.0
	p9
	sS'boolInner'
	p10
	I1
	sS'wallNozzleDwn'
	p11
	V0.00
	p12
	sS'boolSkin'
	p13
	I1
	sS'boolAlt'
	p14
	I0
	sS'zLift'
	p15
	V.3
	p16
	sS'skinNozzleUp'
	p17
	V0.02
	p18
	sS'hopOnlyAtDist'
	p19
	V2
	sS'boolOuter'
	p20
	I1
	sS'liftSpeed'
	p21
	V200
	p22
	ssS'filename'
	p23
	S'DamnFirstLayer_v0.2_share.py'
	p24
	sa.
object_center_x = -1
object_center_y = -1

[alterations]
start.gcode = M106 S101

	G1 F6000

	G91

	G1 Z5
	M140 S{print_bed_temperature}
	M109 S{print_temperature}
	M190 S{print_bed_temperature}
	G21
	G90
	M82
	M107
	M117 Homing X&Y
	G28 X Y
	M203 X4 Y4
	G28 X Y
	G92 X98.5 Y98.5
	M502
	G1 F6000
	G1 X0 Y0
	M117 Homing Z
	G28 Z
	M203 Z.2
	M104 S0
	M140 S0
	G28 Z
	M140 S{print_bed_temperature}
	M104 S{print_temperature}
	M502

	;Fine Tune Z offset positive moves bed closer to nozzle

	G92 Z0.00 

	;Fine Tune Z offset positive moves bed closer to nozzle

	G1 X0 Y0 Z0
	G92 Z0.73
	G1 Z0
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

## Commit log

2015-10-26 Initial Firmware Uploaded
    [Configuration.h, Configuration_adv.h, Marlin Logo.dxf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]
2015-10-26 Added some STL Files
2015-10-26 Create Why have assemblies of parts?
2015-10-26 Update Why have assemblies of parts?
2015-10-26 Add Why have assemblies file
2015-10-26 update why have assemblies
2015-10-26 Changed assemblies files name
2015-10-26 Bill of materials added
    [Printer Kitten BOM (Known Not Accurate, missing and incorrect parts).xlsx]
2015-10-26 BOM Read Me Updated
2015-10-26 BOM Readme Change
2015-10-28 BOM Updated with printed Parts
    [Housing_Front_1.75.STL, Housing_Rear.STL, Printed Part, Spool Holder Part4.STL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]
2015-10-28 Individual STL added
    [Housing_Front_1.75.STL, Housing_Rear.STL, Printed Part, BondTech Clamp 1.STL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]
2015-11-01 general updates
    [Printed Part, Bondtech Housing Front 1.75.STL, Printed Part, Bondtech Housing Rear.STL, Printer Kitten BOM (Known Not Accurate, missing and incorrect parts).xl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]
2015-11-21 11_21_15 Updates Upload
    [Configuration.h, Printer Kitten BOM (Known Not Accurate, missing and incorrect parts).xlsx]
2016-01-18 firmware updates
    [Configuration.h, Configuration_adv.h, Printed Part, Z End Stop Mount.STL]
2016-01-26 STL Updates
    [Printed Part, Corner, Upper Back Right.STL, Printed Part, Corner, Upper Front Left.STL, Printed Part, Corner, Upper Front Right.STL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]
2016-02-01 Firmware and STL updates
    [Configuration.h, Printed Part, IO Mount.STL, Printed Part, Z End Stop Magnet Mount.STL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]
2016-02-05 added cura profile
    [Configuration.h]
2016-02-25 Z-motor Current Reduced
    [Configuration.h, Configuration_adv.h, Marlin Logo.dxf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]
2016-03-24 Major BOM updates and STL updates
    [Bondtech Housing V2 Front 1.75.STL, Bondtech Housing V2 Rear.STL, Printed Part, Corner, Upper Back Right.STL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]
2016-03-31 BOM, Cura Profile, and STL Changes
    [Printed Part, IO Mount Version 2.STL, Printer Kitten BOM.xls, Printer Kitten BOM.xlsx]
2016-03-31 Some Assembly Pictures added
2016-03-31 Initial Assembly instructions
    For building printer from kit, only shows instructions for half of build. Work in progress
2016-04-01 Picture comparing real life and cad kitten
2016-04-04 Assembly Picture Updates
    [Printer Kitten BOM.xls]
2016-04-04 Instructions through complete frame assembly, not done
2016-04-07 Assembly instructions through final assembly
2016-04-11 Make it more clear which size pulley should be used for X and Y axis motors
2016-04-11 Fix broken insertion of picture for upper front left corner final assembly (case-sensitive file name)
2016-04-11 Added bag location for XY end stop magnets
2016-04-11 Clarify the distinction between the screws used for the X and Y motor belt assemblies
2016-04-11 Correct the quantity of screws needed for assembling the spool holder subassembly
2016-04-11 Added bag designation for socket cap screws in the instructions for installing the flange bearings
2016-04-11 Correct screws that should be used for Z axis motor assembly, and add bag location for them
2016-04-11 Removed broken/unnecessary link to assembly picture in Z axis frame plate assembly instructions
2016-04-11 Fix link to assembly picture in section for attaching X axis motor
2016-04-11 Fix misspelling of "gantry"
2016-04-11 Calibration gcode and cura profile added. Z-axis max speed slowed down.
    [Configuration.h, Configuration_adv.h]
2016-04-18 Added calibration pics
2016-04-18 Added calibration instructions
2016-04-18 Removed first print instructions
2016-04-18 Added first print readme
2016-04-18 added link to calibration
2016-04-18 removed reference to power cycle
2016-05-26 folder name changes, bed plates 3D files added
    [Bondtech Housing V2 Front 1.75.STL, Bondtech Housing V2 Rear.STL, Printed Part, BondTech Clamp 1.STL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]
2016-07-19 Revert "folder name changes, bed plates 3D files added"
    This reverts commit 427868cdb3a942e1c04c3b027f78a53edea826db.
    [Bondtech Housing V2 Front 1.75.STL, Bondtech Housing V2 Rear.STL, Printed Part, BondTech Clamp 1.STL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]
2016-07-19 Firmware updates
    3mm steps/mm changed and x, y motor currents decreased
    [Configuration.h]
2016-08-03 Firmware Updates
    Reduced X and Y motor driver currents
    [Configuration.h]
2016-08-22 STL Updates for Titan
    [Printed Part, Titan Mount.STL]
2016-08-22 Updates for Titan
    [Printed Part, Titan Mount.STL]
2016-12-27 Steps per mm extruder updated
    [Configuration.h]
2016-12-27 Folder Structure + Bed Plates
    Folder Structure Changed and Bed Plate Files Added
    [Bondtech Housing V2 Front 1.75.STL, Bondtech Housing V2 Rear.STL, Print Assembly 3 Z Axis.STL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]
2018-10-29 Solid Model File of Entire Printer Assembly added
